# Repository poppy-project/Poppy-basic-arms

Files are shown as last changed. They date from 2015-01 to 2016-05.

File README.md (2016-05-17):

Poppy simple humanoid arms
===================

This Poppy module include CAD models and assemblies for 3D printable parts to create left and right basic 4 DoFs robotic humanoid arms.

It can be used for the [Poppy Humanoid](https://github.com/poppy-project/poppy-humanoid) or be freely included in any other robotic creatures if you find it relevant.

### Left arm:
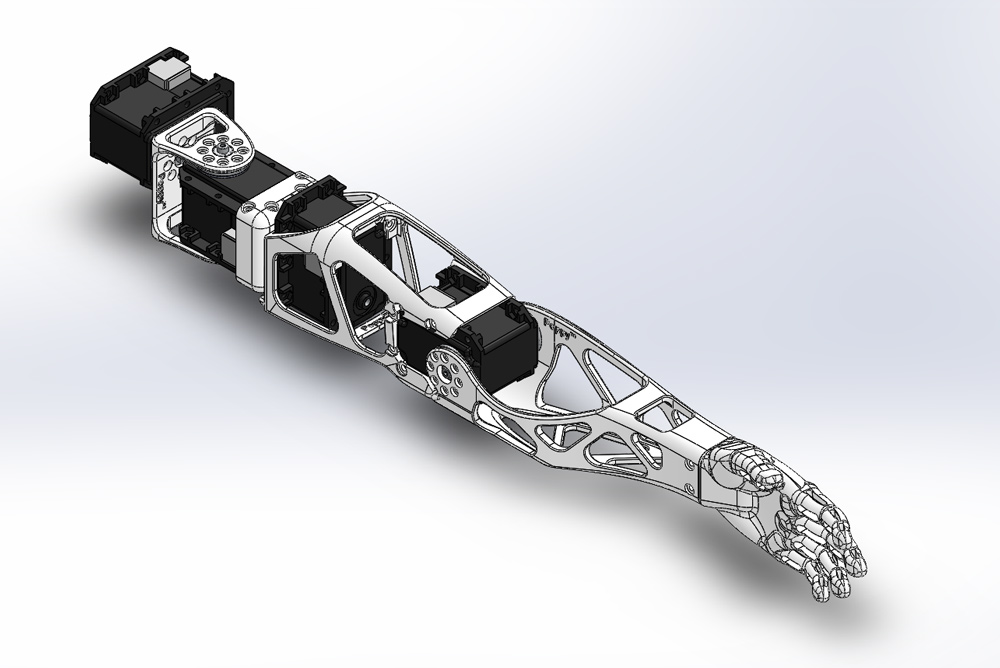
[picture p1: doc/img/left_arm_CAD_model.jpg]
left arm


### Right arm:
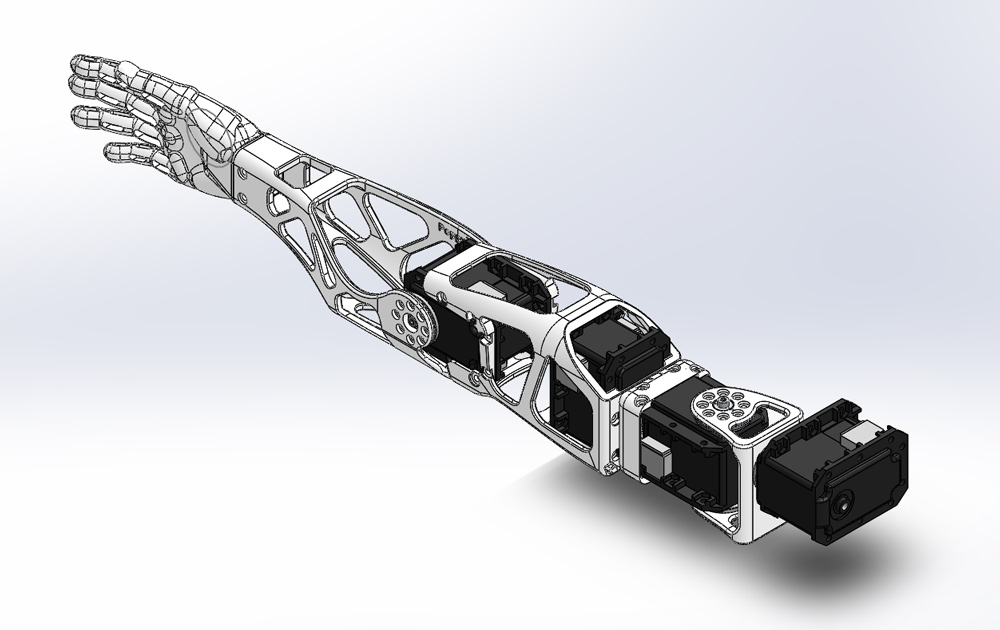
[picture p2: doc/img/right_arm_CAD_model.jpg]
right arm


The design was done using Solidworks (2013-SP5) and is distributed with native formats. More format such as STEP and STL can be found in the [release](releases/) section.

## Open Source Hardware

All the technological development work made in the Poppy project is freely available under open source licenses. Only the name usage *"Poppy"* is restricted and protected as an international trademark, please contact us if you want to use it or have more information.

 **This work is licensed under a [Creative Commons Attribution-ShareAlike 4.0 International License](http://creativecommons.org/licenses/by-sa/4.0/).**
Please keep references to the Poppy project (www.poppy-project.org) and authors when you use or fork this work.

**Authors:** Matthieu Lapeyre, Alexandre Le Falher.

### Looking for the Solidworks files ?

We are using a GitHub feature called GIT LFS. It is great for versionning solidworks files but it stills lack basic features. If you download directly solidworks files from this web page, you will get an empty file...

You have two option:

1. Download the last official Solidworks version in the [release](https://github.com/poppy-project/Poppy-basic-arms/releases). You will also find STL, STEP and parasolid files.
- Clone locally this repository following [this guide](doc/cloning.md). This solution is only for people desiring to contribute or develop news hardware features for Poppy.

## Support
You need support ?
The [Poppy forum](forum.poppy-project.org) is the best (and single) place to ask for help !

## Setup

This module requires the [Robotis Library](https://github.com/matthieu-lapeyre/Robotis-library), which includes all Robotis components needed for the actuation of these arms.

## Contribute

### /!\ SolidWorks version
The SolidWorks policy sucks, they intentionnaly break compatibility between recent and older version. If you have a Solidworks older than 2013-SP0 you will certainly be able to open these parts but only as a read-only mode, which is equivalent to not beign able to open it...

Therefore, we won't upgrade our SolidWorks so more people can easily modify parts for their own uses.

For the same reason, we ask potential contributors wanting to pull work into official repository to downgrade (if needed) their solidworks version to 2013.

Accepting a pull-request from a Soldiworks >= 2014 will break whole compatibility.

## The Poppy project history

The Poppy project is born in 2012 in the [Flowers laboratory](flowers.inria.fr) at [Inria Bordeaux Sud-Ouest](http://www.inria.fr/en/centre/bordeaux).
It was initiated during [Matthieu Lapeyre](github.com/matthieu-lapeyre)'s PhD Thesis surpervised by [Pierre Yves Oudeyer](http://www.pyoudeyer.com/). At the beginning, the development team was composed by Matthieu Lapeyre (mechanics & design), [Pierre Rouanet](github.com/pierre-rouanet) (software) and [Jonathan Grizou](http://jgrizou.com/) (electronics).

This project is initially a fundamental research project financed by [ERC Grant Explorer](http://erc.europa.eu/) to explore the role of embodiement and morphology properties on cognition and especially on the learning of sensori-motor tasks.

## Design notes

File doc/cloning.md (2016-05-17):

# Cloning this repository

Git and Github are designed for versioning code, using it as a versioning platform for hardware files is a bit out of the scope this tools are made for.

Therefore, we use quite advanced git features such as Submodules and Git LFS.

## Installation

To clone this repository, you need both Git and Git LFS.

1. [Installing Git](https://git-scm.com/book/en/v2/Getting-Started-Installing-Git)
- [Installing GIT LFS](https://help.github.com/articles/installing-git-large-file-storage/#platform-windows)

### [Optional] Install Source Tree

Source Tree is a software providing a nice and easy to use interface for Git. If you are not familiar with Git, it helps a lot understanding what the hell happens.

You can download it [here](https://www.sourcetreeapp.com/)

## Clone this repository

Once you have installed every soft needed, you can "clone" the repository.

### Using Source Tree

Configure your app, then click on the **new repository** button and specify the url of this repository `https://github.com/poppy-project/poppy-basic-arms.git`

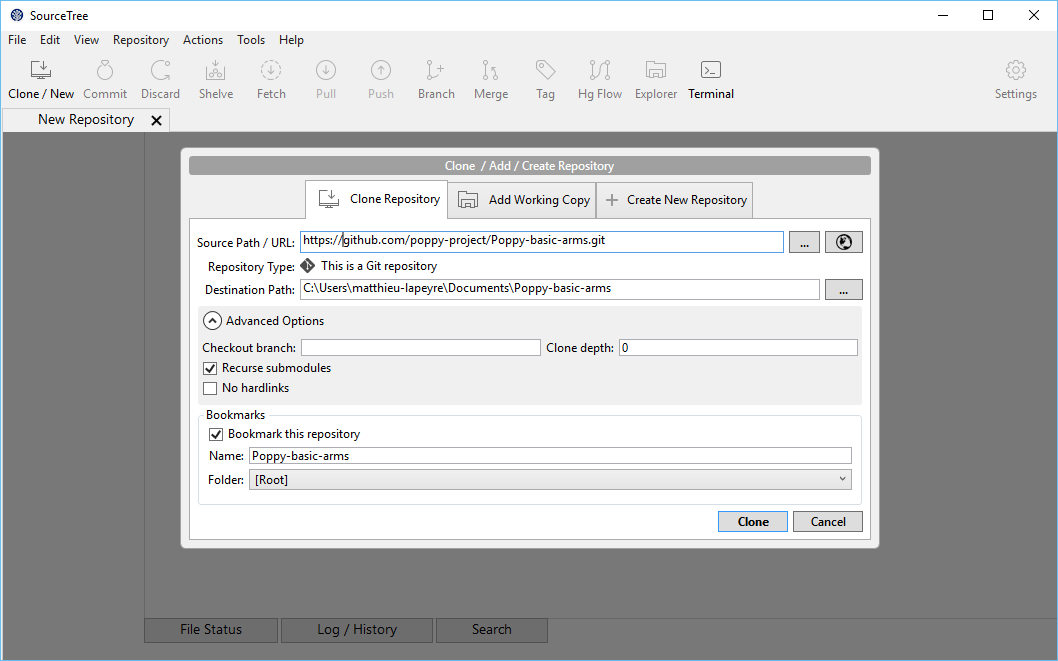
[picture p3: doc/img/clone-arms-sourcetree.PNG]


If you have forked this project, replace the url by your `https://github.com/YOUR-USERNAME/poppy-basic-arms.git`

### Using the Command line

Open your terminal (or Git Bash on Windows) and tape ` git clone --recursive git://github.com/poppy-project/poppy-basic-arms.git`

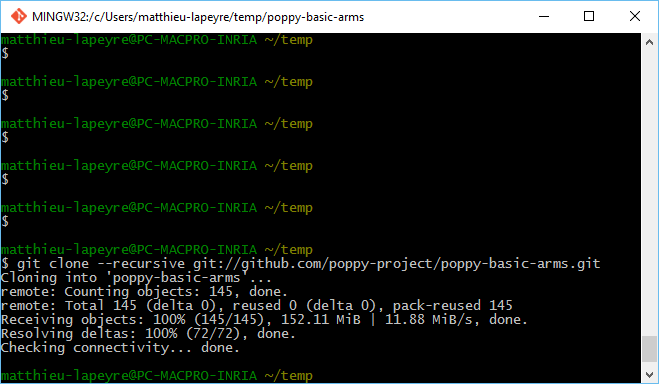
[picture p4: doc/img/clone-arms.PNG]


This will clone the entire repository including all submodules and download all files.

Again, if you have forked the repository, change the url accordingly.

## Clone the Robotis Library repository

The Poppy arms uses Robotis motors. You've maybe see the robotis model are not here. Actually you have to clone them also.

### Using Source Tree

Same method but this time use the following Source path: `https://github.com/poppy-project/robotis-library.git`

### Using the Command line

Open your terminal (or Git Bash on Windows) and tape ` git clone --recursive git://github.com/poppy-project/robotis-library.git`

## Open the assembly

Now you can open the *humanoid_arm.SLDASM* file and you may have to specify where are the Robotis model. Just indicate the folder in which you have cloned the repository.

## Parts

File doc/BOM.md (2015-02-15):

## Bill of Material:

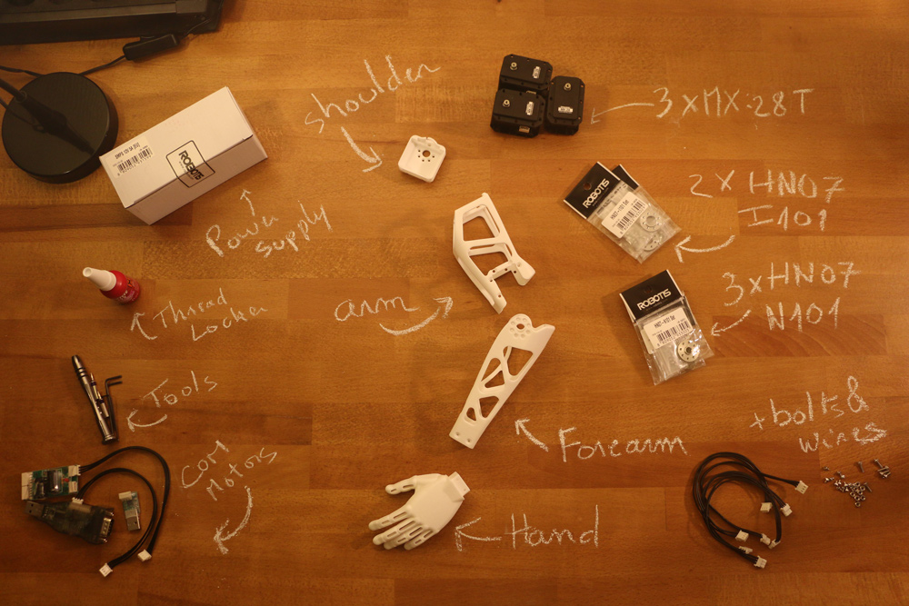
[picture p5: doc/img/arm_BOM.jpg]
Arm BOM


**3D Printed**:
- Hand (left or right)
- Forearm (left or right)
- Upper arm *(displayed arm on picture)*
- Arm connector *(displayed shoulder on picture)*

**Actuators:**
- 3x Robotis Dynamixel MX28-AT (or MX28-T)

**Robotis parts:**
- 3x HN07-N101
- 2x HN07-I101

**Motor configuration:**
- 1x Alimentation 12V
- 1x SMPS2Dynamixel
- 1x USB2Dynamixel or USB2AX
- A computer...

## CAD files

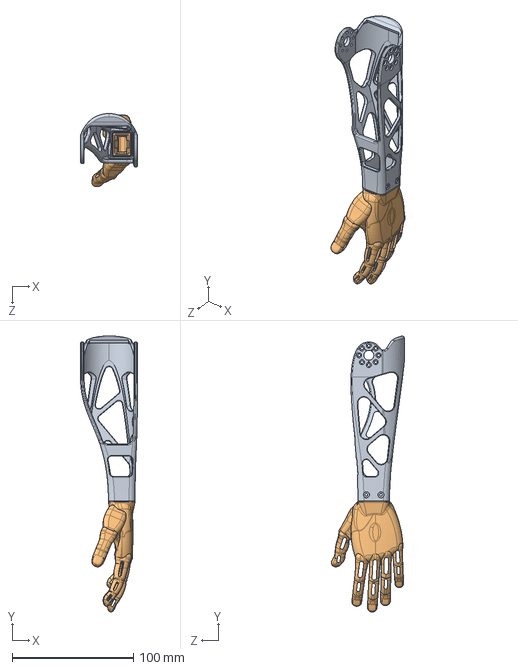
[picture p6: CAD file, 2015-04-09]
subassemblies/forearm.SLDASM
47.0 x 227.5 x 60.1 mm
forearm
hand

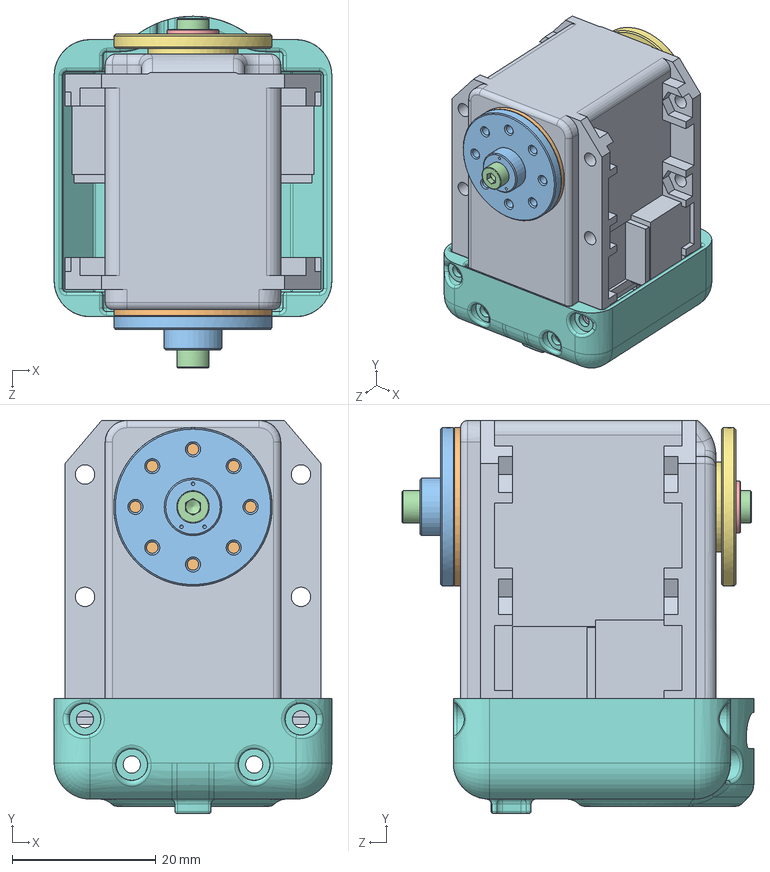
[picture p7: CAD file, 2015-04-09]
subassemblies/shoulder_x.SLDASM
38.6 x 54.6 x 48.8 mm
dynamixel_x28series
trust_washer
HN07-N101
WB_M2.5x8 x 2
RX28-CAP
MF106ZZ
HN07-i101
arm_connector

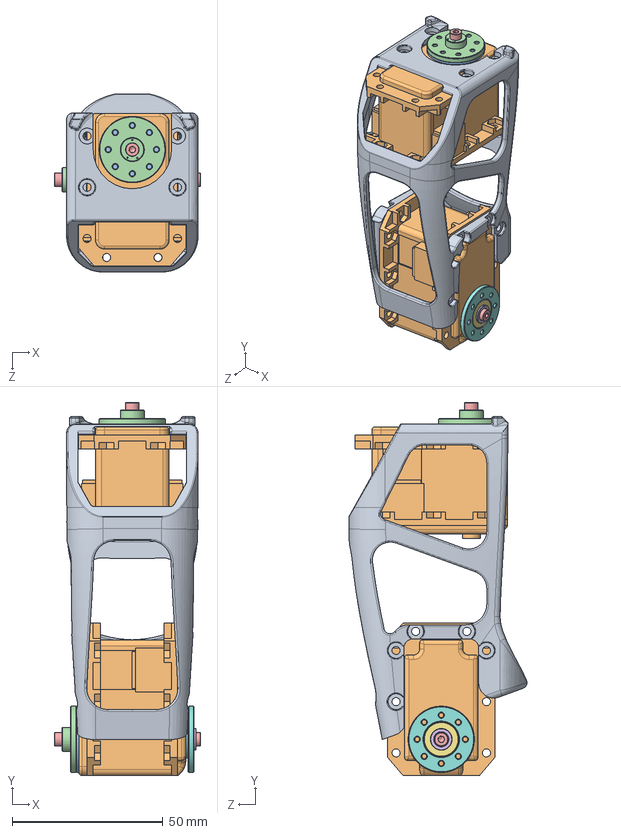
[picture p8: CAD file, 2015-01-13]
subassemblies/upper_arm.SLDASM
48.5 x 123.8 x 59.1 mm
upper_arm
dynamixel_x28series x 2
trust_washer x 2
HN07-N101 x 2
WB_M2.5x8 x 3
RX28-CAP
MF106ZZ
HN07-i101

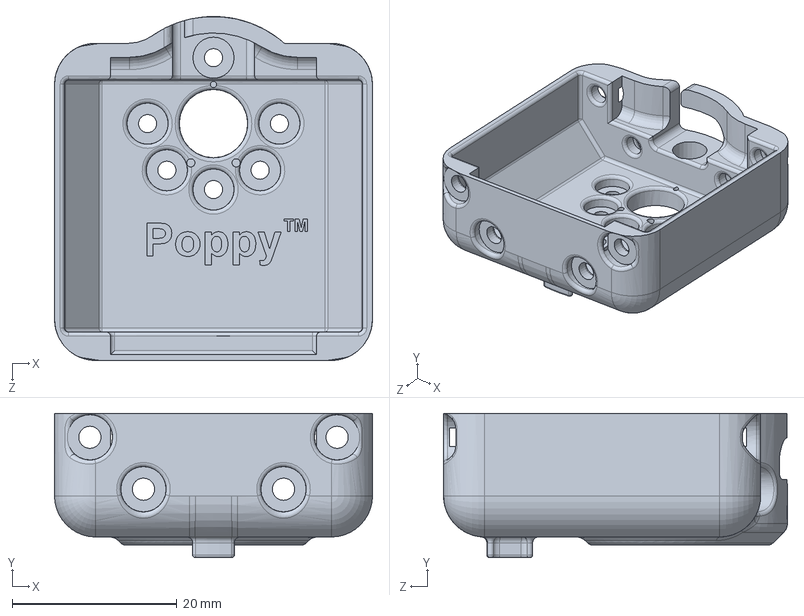
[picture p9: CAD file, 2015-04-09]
parts/arm_connector.SLDPRT
38.6 x 17.5 x 41.8 mm

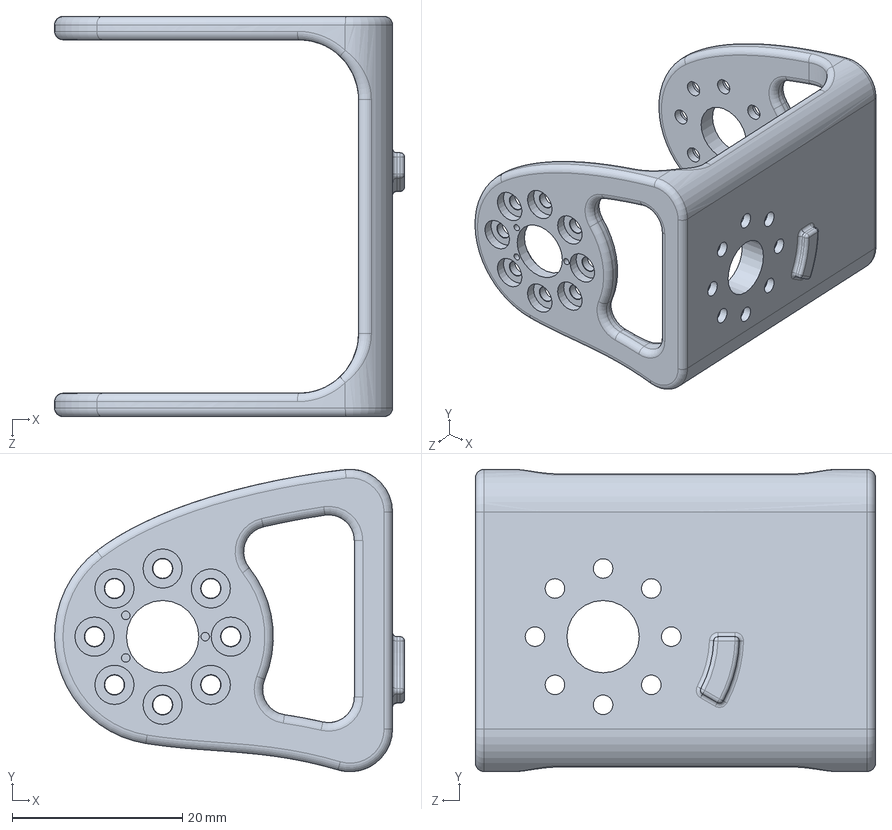
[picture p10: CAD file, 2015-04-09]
parts/shoulder.SLDPRT
41.1 x 35.5 x 47.0 mm

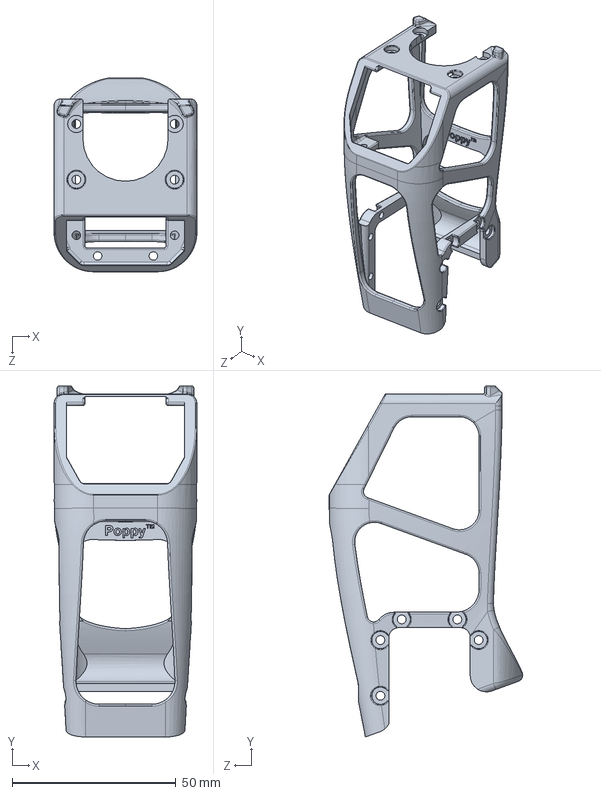
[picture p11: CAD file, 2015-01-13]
parts/upper_arm.SLDPRT
43.6 x 107.1 x 59.1 mm

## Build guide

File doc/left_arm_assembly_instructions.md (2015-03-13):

# Left arm assembly instructions

## 1- Get all components required

First ensure you have all components detailed in the [Bill Of Material](BOM.md).
Also as a friendly reminder, do not forget to use threadlocker otherwise you will see your robot disassemble itself after just few weeks due to vibration.

## 2- Build sub-assemblies

First you need to assemble several sub-assemblies which will be combined to create the multi-articulated arm

The following instructions will guide you in this assembly process:

- **1.1- [Left Forearm ](subassemblies/left_forearm_assembly_instructions.md)**
- **1.2- [Left upper arm](subassemblies/left_upper_arm_assembly.md)**
- **1.3- [Left upper-arm/shoulder](subassemblies/left_upper_arm_shoulder_assembly.md)**

## 3- Left arm assembly

- Preparation: 5 min
- Assembly: 5-10 min

### 3.1- Requirement:
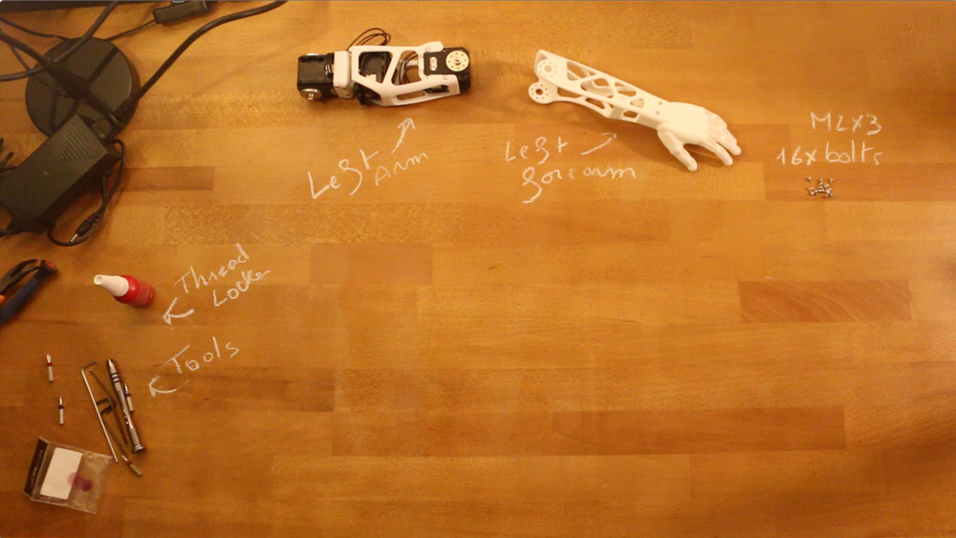
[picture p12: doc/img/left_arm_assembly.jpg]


**Subassembly**:
- Right upper arm
- Right forearm

**Robotis parts:**
- 16x Bolts M2x3

### 3.2- Assembly instructions:

- **Step 1:** Ensure you have read [**this note**](//github.com/poppy-project/Robotis-library/blob/master/doc/en/robotis_tricks.md) before continuing to avoid the classic (and critical) traps when using Robotis Dynamixel actuators.
- **Step 2**: Click on the image below to display the video:
(http://youtu.be/TZb6_hVlmcA)

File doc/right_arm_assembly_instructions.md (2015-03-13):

# Right Arm assembly instructions

## 1- Get all components required

First ensure you have all components detailed in the [Bill Of Material](BOM.md).
Also as a friendly reminder, do not forget to use threadlocker otherwise you will see your robot disassemble itself after just few weeks due to vibration.

## 2- Build sub-assemblies

First you need to assemble several sub-assemblies which will be combined to create the multi-articulated arm

The following instructions will guide you in this assembly process:

- **1.1- [Right Forearm ](subassemblies/right_forearm_assembly_instructions.md)**
- **1.2- [Right upper arm](subassemblies/right_upper_arm_assembly.md)**
- **1.3- [Right upper-arm/shoulder](subassemblies/right_upper_arm_shoulder_assembly.md)**

## 3- Right arm assembly

- Preparation: 5 min
- Assembly: 5-10 min

### 3.1- Requirement:
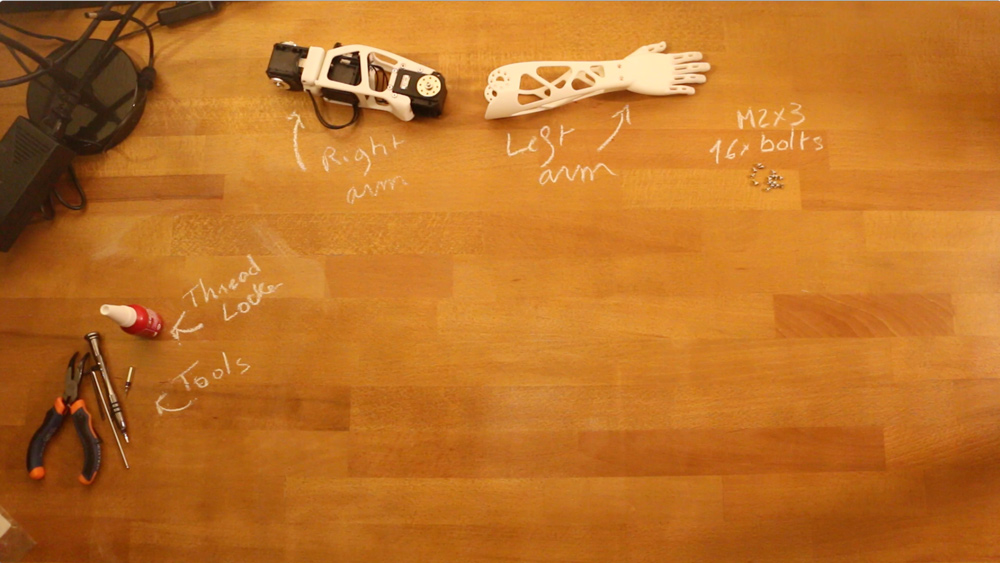
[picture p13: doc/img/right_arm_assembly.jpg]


**Subassembly**:
- Right upper arm
- Right forearm *(displayed left arm on picture)*

**Robotis parts:**
- 16x Bolts M2x3

### 3.2- Assembly instructions:

- **Step 1:** Ensure you have read [**this note**](//github.com/poppy-project/Robotis-library/blob/master/doc/en/robotis_tricks.md) before continuing to avoid the classic (and critical) traps when using Robotis Dynamixel actuators.
- **Step 2**: Click on the image below to display the video:

(http://youtu.be/Oe5v21sTst8)

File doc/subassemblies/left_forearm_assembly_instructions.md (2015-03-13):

# Left Forearm assembly instructions

- Preparation: 5 min
- Assembly: 5-10 min

## Requirement:
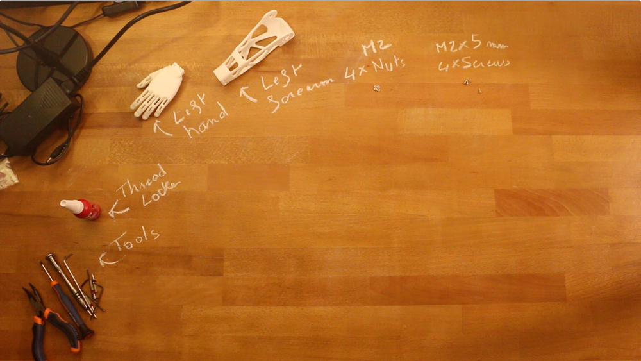
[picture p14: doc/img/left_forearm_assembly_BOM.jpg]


**3D Printed parts**:
- Left hand
- left Forearm

**Robotis parts:**
- 4x Nuts M2
- 4x Screws M2

## Assembly instructions:

- **Step 1:** Ensure you have read [**this note**](//github.com/poppy-project/Robotis-library/blob/master/doc/en/robotis_tricks.md) before continuing to avoid the classic (and critical) traps when using Robotis Dynamixel actuators.
- **Step 2**: Click on the image below to display the video:
(http://youtu.be/5FsPgEt4cfA)

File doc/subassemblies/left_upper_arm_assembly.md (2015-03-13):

# Left upper arm assembly instructions

- Preparation: 10 min
- Assembly: 20-30 min

## Requirement:
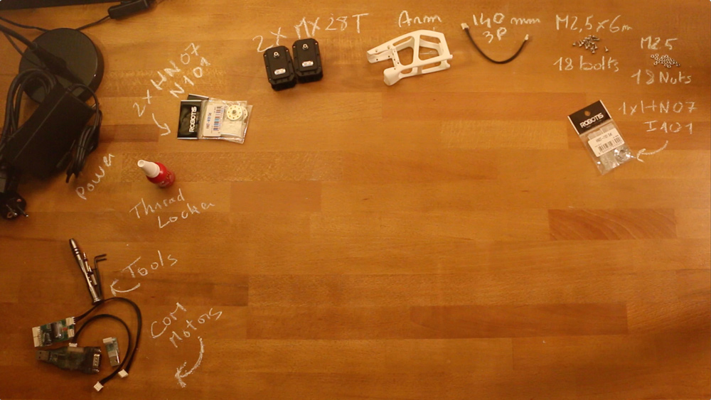
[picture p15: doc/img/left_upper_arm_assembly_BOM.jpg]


**3D Printed parts**:
- Upper arm *(displayed arm on picture)*

**Actuators:**
- 2x Robotis Dynamixel MX28-AT (or MX28-T)

**Cables**:
- 2x 3P 140mm

**Robotis parts:**
- 2x HN07-N101
- 1x HN07-I101
- 18x Nuts M2.5
- 18x Bolts M2.5x6

**Motor configuration:**
- 1x Alimentation 12V
- 1x SMPS2Dynamixel
- 1x USB2Dynamixel or USB2AX
- A computer...

## Assembly instructions:

- **Step 1:** Ensure you have read [**this note**](//github.com/poppy-project/Robotis-library/blob/master/doc/en/robotis_tricks.md) before continuing to avoid the classic (and critical) traps when using Robotis Dynamixel actuators.
- **Step 2**: Click on the image below to display the video:
(http://youtu.be/MIjfAXShLJ4)

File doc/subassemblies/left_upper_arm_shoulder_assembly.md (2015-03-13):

# Left upper-arm/shoulder assembly instructions

- Preparation: 10 min
- Assembly: 15-20 min

## Requirement:
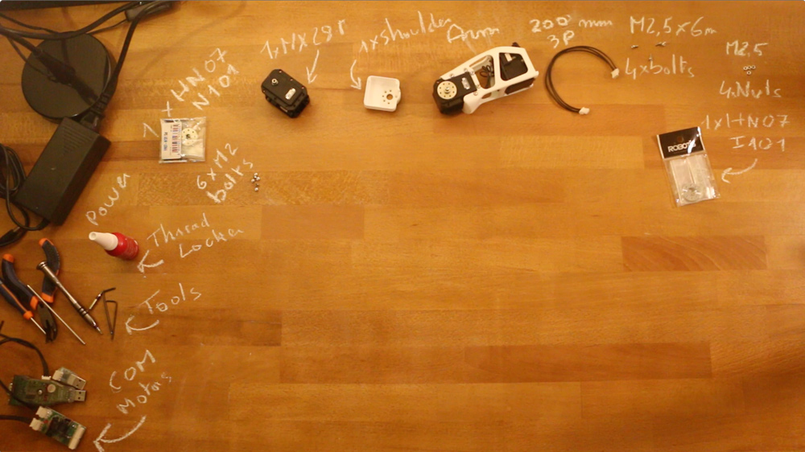
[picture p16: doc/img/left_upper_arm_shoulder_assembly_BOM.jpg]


**Subassembly**:
- Left upper arm *(displayed arm on picture)*

**3D Printed parts**:
- arm connector *(displayed shoulder on picture)*

**Actuators:**
- 1x Robotis Dynamixel MX28-AT (or MX28-T)

**Cables**:
- 1x 3P 200mm

**Robotis parts:**
- 1x HN07-N101
- 1x HN07-I101
- 8x Nuts M2.5
- 8x Bolts M2.5x6
- 6x Bolts M2x3

**Motor configuration:**
- 1x Alimentation 12V
- 1x SMPS2Dynamixel
- 1x USB2Dynamixel or USB2AX
- A computer...

## Assembly instructions:

- **Step 1:** Ensure you have read [**this note**](//github.com/poppy-project/Robotis-library/blob/master/doc/en/robotis_tricks.md) before continuing to avoid the classic (and critical) traps when using Robotis Dynamixel actuators.
- **Step 2**: Click on the image below to display the video:
(http://youtu.be/qCF_8-M5k1o)

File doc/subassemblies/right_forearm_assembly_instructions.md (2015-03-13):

# Right Forearm assembly instructions

- Preparation: 5 min
- Assembly: 5-10 min

## Requirement:
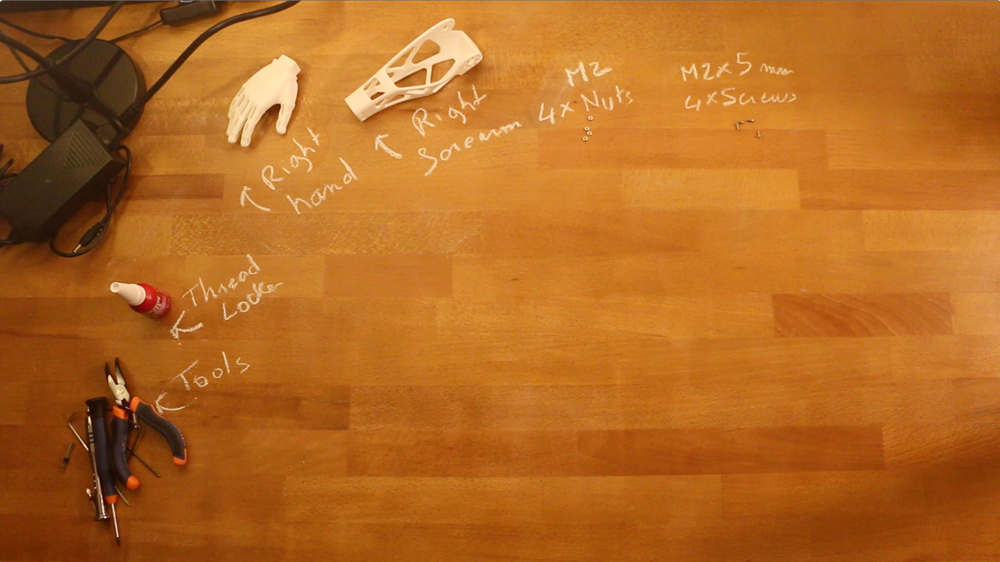
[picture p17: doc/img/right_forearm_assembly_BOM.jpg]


**3D Printed parts**:
- Right hand
- Right Forearm

**Robotis parts:**
- 4x Nuts M2
- 4x Screws M2

## Assembly instructions:

- **Step 1:** Ensure you have read [**this note**](//github.com/poppy-project/Robotis-library/blob/master/doc/en/robotis_tricks.md) before continuing to avoid the classic (and critical) traps when using Robotis Dynamixel actuators.
- **Step 2**: Click on the image below to display the video:
(http://youtu.be/SUlM_mE3plc)

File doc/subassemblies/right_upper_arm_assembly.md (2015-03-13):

# Right upper arm assembly instructions

- Preparation: 10 min
- Assembly: 20-30 min

## Requirement:
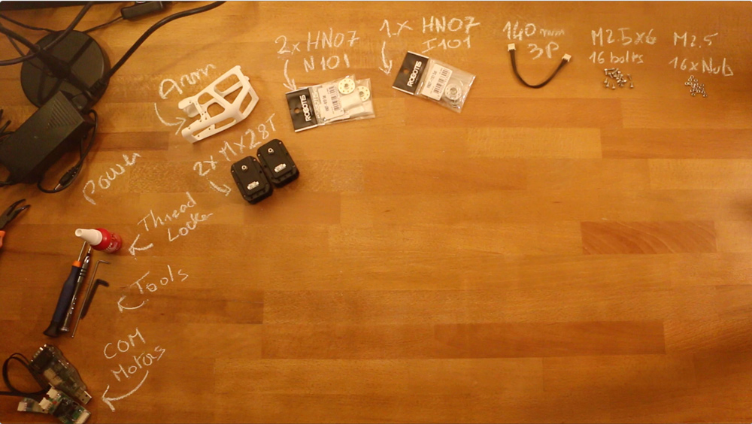
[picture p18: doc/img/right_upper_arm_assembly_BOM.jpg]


**3D Printed parts**:
- Upper arm *(displayed arm on picture)*

**Actuators:**
- 2x Robotis Dynamixel MX28-AT (or MX28-T)

**Cables**:
- 2x 3P 140mm

**Robotis parts:**
- 2x HN07-N101
- 1x HN07-I101
- 18x Nuts M2.5
- 18x Bolts M2.5x6

**Motor configuration:**
- 1x Alimentation 12V
- 1x SMPS2Dynamixel
- 1x USB2Dynamixel or USB2AX
- A computer...

## Assembly instructions:

- **Step 1:** Ensure you have read [**this note**](//github.com/poppy-project/Robotis-library/blob/master/doc/en/robotis_tricks.md) before continuing to avoid the classic (and critical) traps when using Robotis Dynamixel actuators.
- **Step 2**: Click on the image below to display the video:
(http://youtu.be/cYhGwD6r6NQ)

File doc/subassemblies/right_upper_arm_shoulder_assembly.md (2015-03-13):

# Right upper-arm/shoulder assembly instructions

- Preparation: 10 min
- Assembly: 15-20 min

## Requirement:
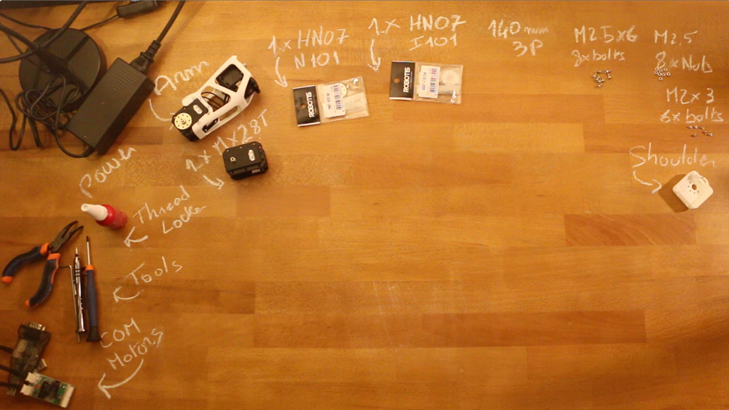
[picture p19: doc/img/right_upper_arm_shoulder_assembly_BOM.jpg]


**Subassembly**:
- Right upper arm *(displayed arm on picture)*

**3D Printed parts**:
- arm connector *(displayed shoulder on picture)*

**Actuators:**
- 1x Robotis Dynamixel MX28-AT (or MX28-T)

**Cables**:
- 1x 3P 200mm

**Robotis parts:**
- 1x HN07-N101
- 1x HN07-I101
- 8x Nuts M2.5
- 8x Bolts M2.5x6
- 6x Bolts M2x3

**Motor configuration:**
- 1x Alimentation 12V
- 1x SMPS2Dynamixel
- 1x USB2Dynamixel or USB2AX
- A computer...

## Assembly instructions:

- **Step 1:** Ensure you have read [**this note**](//github.com/poppy-project/Robotis-library/blob/master/doc/en/robotis_tricks.md) before continuing to avoid the classic (and critical) traps when using Robotis Dynamixel actuators.
- **Step 2**: Click on the image below to display the video:
(http://youtu.be/BdQcOAwZbMY)

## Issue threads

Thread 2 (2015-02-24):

several bug on the arm connector.

matthieu-lapeyre, 2015-02-24:
- [x] increase head size diameter for M2 and M2.5 bolts
- [x] increase the blocking system size by 0.5-1mm
- [x] increase distance between the the shoulder_x and arm_z motor by 1-2mm

Closed 2015-02-27.

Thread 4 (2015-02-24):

Thickness under bolt head M2 thickness

matthieu-lapeyre, 2015-02-24:
Reduce it from 1.5 to 1.2-1.3mm to ensure the M2x3 correct fixation.

Closed 2015-02-27.

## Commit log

2015-01-13 add all 3D printed parts to build a humanoid like robotic arm with both left and right configuration.
    [arm_connector.SLDPRT, shoulder.SLDPRT, upper_arm.SLDPRT]
2015-01-13 add assemblies of custom 3D printed part with Robotis Dynamixel actuators. Require to download the robotis_library CAD repository.
    [forearm.SLDASM, shoulder_x.SLDASM, upper_arm.SLDASM]
2015-01-13 add the full assembly of a 4 DoF robotic arm with both right and left configuration
2015-02-15 add CAD screenshot and update readme
2015-02-15 add bill of material
2015-02-15 add assembly instructions
2015-02-16 fix refs for the right arm documentation
2015-02-16 fix refs for the left arm assembly documentation
2015-02-19 update documentation to include stuffs about the Robotis Dynamixel assembly
2015-02-21 add link to the BOM
2015-02-27 - increase blocking system by 0.5mm - increase holes diameter - increase the assembly tolerance with the shoulder_x motor Fix #2
    [arm_connector.SLDPRT]
2015-02-27 change M2 counterbore thickness. Issue #4 Fix #4
    [shoulder.SLDPRT]
2015-04-09 update material properties
    [arm_connector.SLDPRT, forearm.SLDASM, shoulder.SLDPRT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]
